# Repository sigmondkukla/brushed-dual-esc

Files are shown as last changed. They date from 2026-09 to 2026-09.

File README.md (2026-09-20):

# brushed-dual-esc
**Clarkson University Combat Robotics SPEED Team**

## Summary

Dual drive ESC for Clarkson Combat Robotics 1lb freshman PLAnt competition.
Supports two 3A brushed drive motors and includes a 5V 1A BEC output to power a receiver. 

## Details

The ESC implements an STM32C011 MCU to generate PWM for motor drivers from RX channel inputs while monitoring current, signal prescence (failsafe), and battery voltage UVLO.

With the 2026 revision of the ESC, XT30 wire-to-board connectors have been replaced with solder pads for leads to GNB A30 connectors.
An XT30 connector is still reccomended for the battery input.
The battery shall be a 2S or 3S LiPo battery; 4S is not supported based on cost optimization, though targeting a slightly higher cost (and larger size) by increasing capacitor specifications is a simple modification.
At 4S, the current from the 5V BEC output shall be kept to a minimum. 

The ESC expects two receiver channel outputs to be connected to the CH1 and CH2 inputs, which map directly to the DRV1 and DRV2 outputs. A 50 Hz (20 ms period) PWM signal (5V tolerated) with a duty cycle between 1000 us and 2000 us is needed, based on the outputs of the common FS-2A receiver.
A duty cycle of 1500 us is considered neutral, with lower duty cycles resulting in reverse operation and higher duty cycles corresponding to forward operation.

A 3A current limit has been configured with the 750-ohm resistors connected to IPROPI on each motor driver.
Above this current limit, the ESC will chop to avoid over current, despite the driver supporting up to 3.7A.
The ESC pairs well therefore with the [Repeat Mini Brushed Mk2](https://repeat-robotics.com/products/repeat-mini-brushed-mk2-1pcs), which has a stall current of 2A at 3S.

## Assembly

Assembly with a pick-and-place machine is reccomended for large volumes >= 10 units, though hand assembly is straightforward given the large motor driver, LDO, and passives packages.
The pick and place work file for a CHM-T36VA machine is included in the `pcb/fabrication` directory, though minor modifications may be necessary.
The DRV8231 ICs were not successfully picked by the machine so are set to be skipped, and the electrolytic capacitors were not attempted.
I loaded the 503 nozzle in tool 1 and the 505 nozzle in tool 2 for this job.

A clean paste image is necessary for successful soldering of the STM32 MCU.

## Programming

Programming is achieved through a Tag-Connect TC2030-CTX-NL pogo pins programmer cable which retails around $50, though can be purchased on Aliexpress for about half the price.
I'm using it in conjunction with a Segger J-Link EDU mini though any debugger can be used.
SWO is not available on STM32C0 so one of the six pins is unused.

The firmware may be programmed using [STM32CubeProg](https://www.st.com/en/development-tools/stm32cubeprog.html) and the firmware ELF file included in the most recent release on GitHub.

## Images
### Screenshots
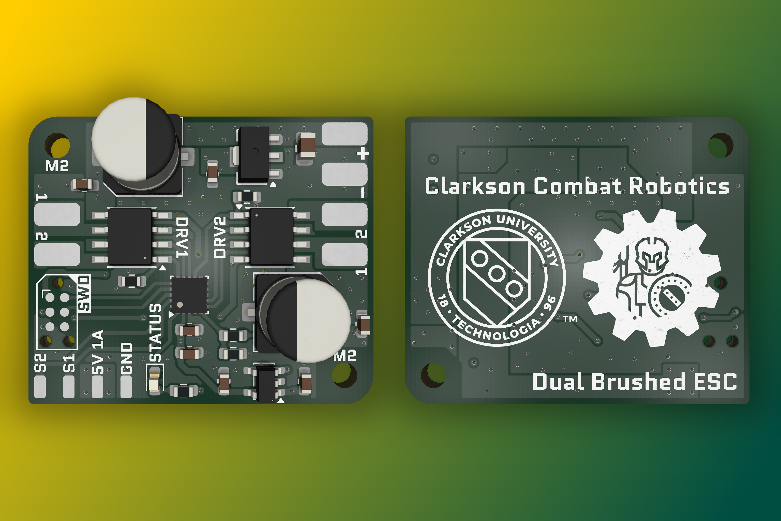
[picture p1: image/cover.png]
Cover

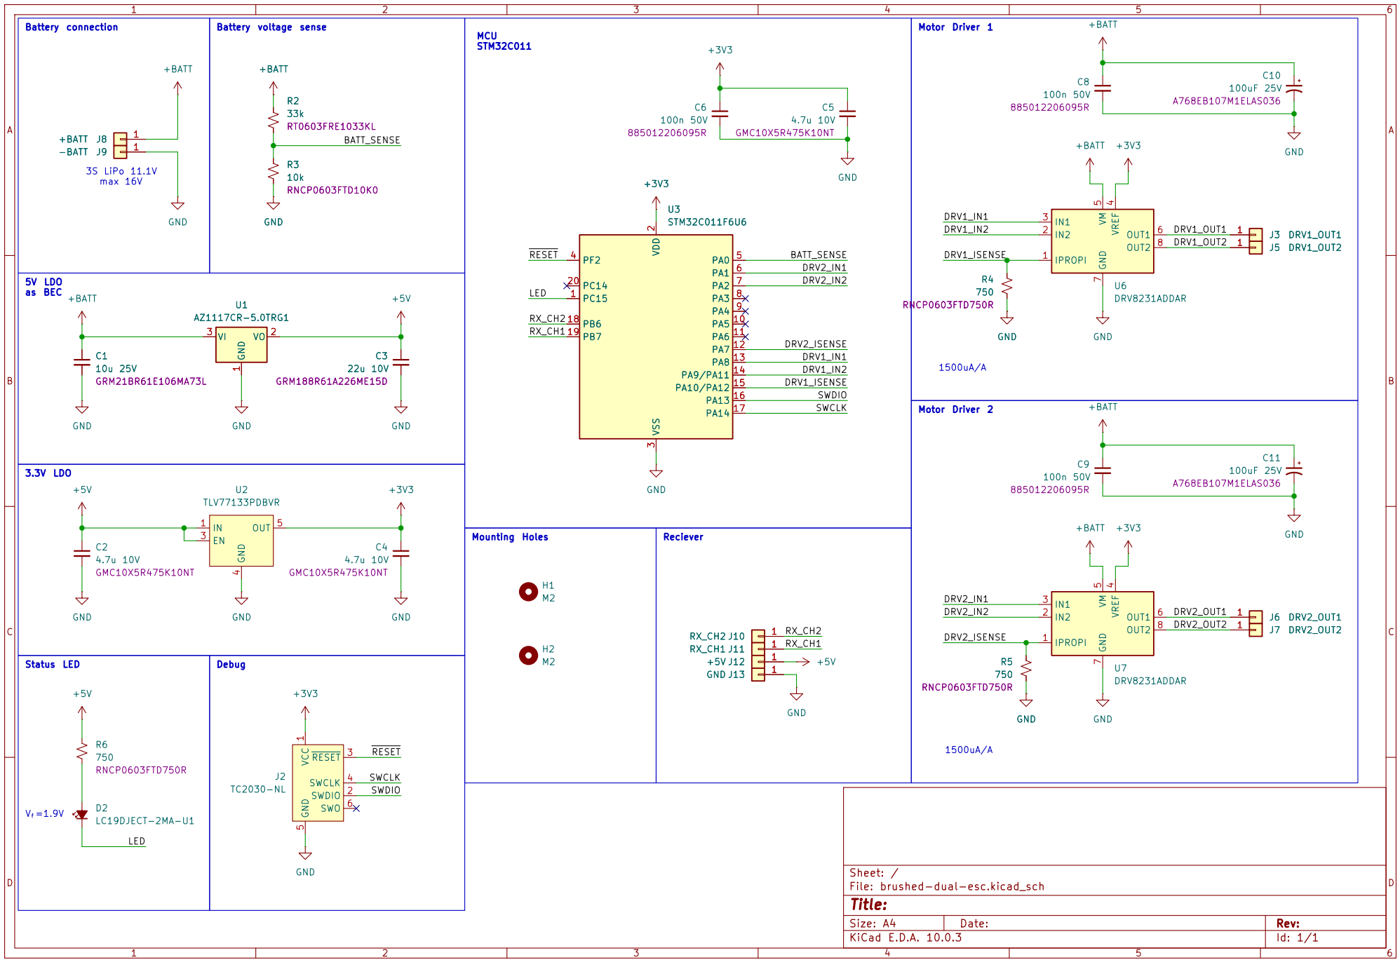
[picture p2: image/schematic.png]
Schematic diagram

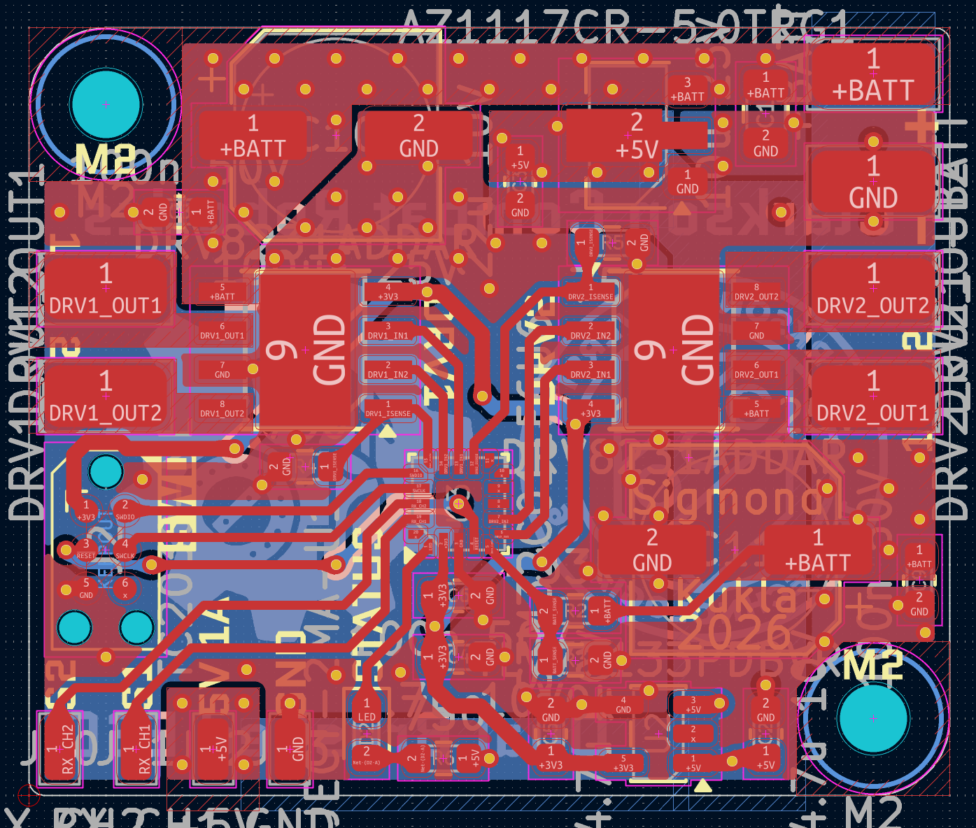
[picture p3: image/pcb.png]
PCB top layer


### Photos
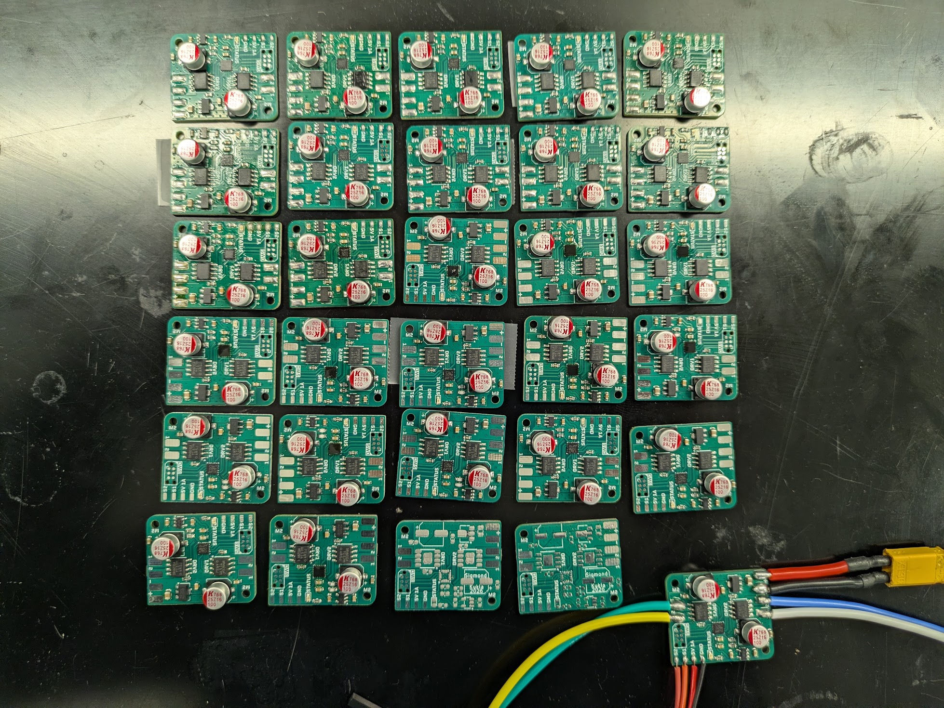
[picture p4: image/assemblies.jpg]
Assemblies


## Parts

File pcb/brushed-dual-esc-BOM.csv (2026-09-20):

Reference | Qty | Value | MPN
C1 | 1 | 10µF 25V | GRM21BR61E106MA73L
C2,C4,C5 | 3 | 4.7u 10V | GMC10X5R475K10NT
C3 | 1 | 22uF 10V | GRM188R61A226ME15D
C6,C8,C9 | 3 | 100n 50V | 885012206095R
C10,C11 | 2 | 100uF 25V | A768EB107M1ELAS036
D2 | 1 | Vf=1.9V | LC19DJECT-2MA-U1
R2 | 1 | 33k | RT0603FRE1033KL
R3 | 1 | 10k | RNCP0603FTD10K0
R4,R5,R6 | 3 | 750 | RNCP0603FTD750R
U1 | 1 | AZ1117CR-5.0TRG1 | AZ1117CR-5.0TRG1
U2 | 1 | TLV77133PDBVR | TLV77133PDBVR
U3 | 1 | STM32C011F6U6 | STM32C011F6U6
U6,U7 | 2 | DRV8231ADDAR | DRV8231ADDAR

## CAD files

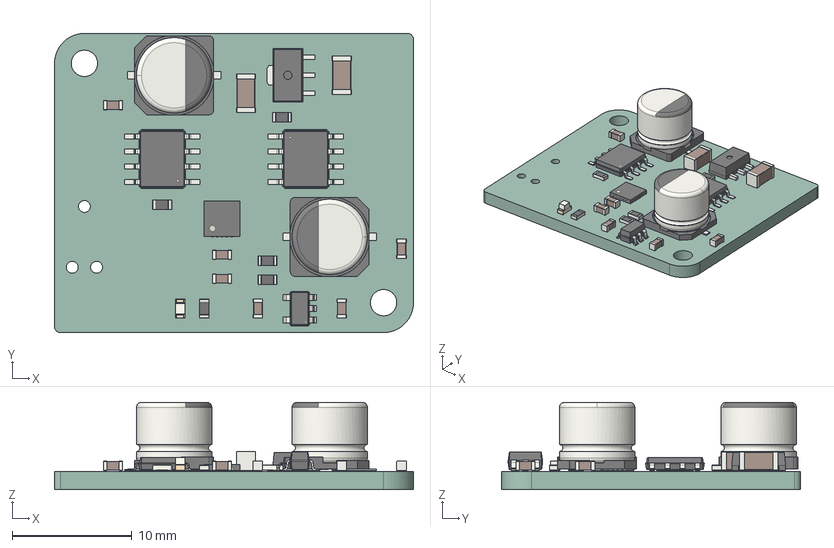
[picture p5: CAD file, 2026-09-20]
pcb/brushed-dual-esc.step
30.0 x 25.0 x 7.29 mm
R_0603_1608Metric x 5
C_0603_1608Metric x 6
CP_Elec_63x57 x 2
HSOP-8-1EP_3.9x4.9mm_P1.27mm_EP2.41x3.1mm x 2
LED_0603_1608Metric
SOT-23-5
C_1206_3216Metric x 2
UQFN-20-1EP_3x3mm_Pitch0.4mm
adbeea57-9c39-11ed-93f0-dde97e994e83_part
adbeea58-9c39-11ed-93f0-dde97e994e83_part
adbeea59-9c39-11ed-93f0-dde97e994e83_part
brushed-dual-esc_PCB

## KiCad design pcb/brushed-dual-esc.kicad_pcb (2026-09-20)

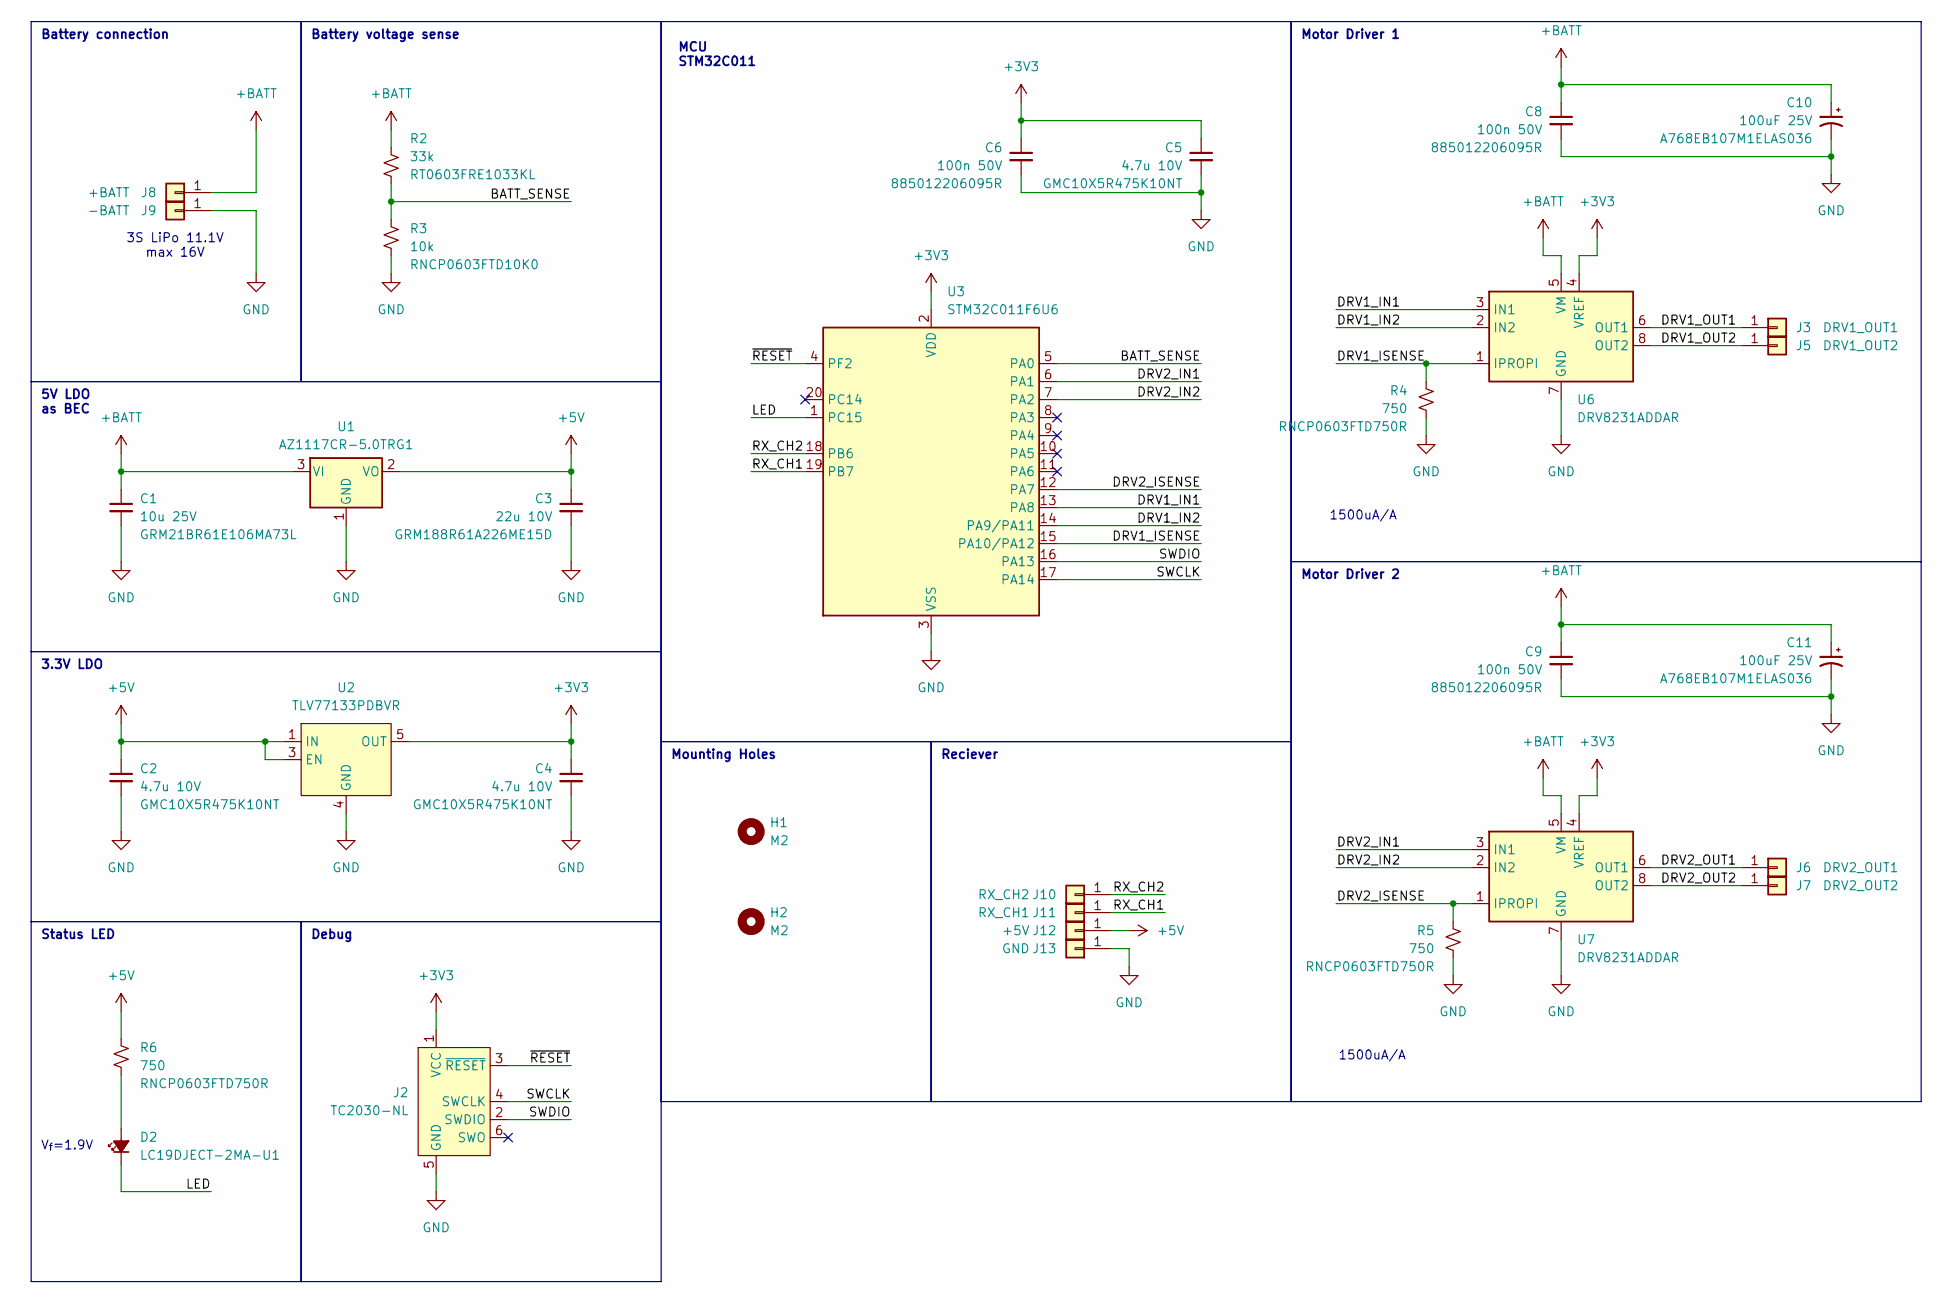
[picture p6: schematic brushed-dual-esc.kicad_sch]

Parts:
C1: 10u 25V; C_0805_2012Metric; MPN GRM21BR61E106MA73L
C2, C4, C5: 4.7u 10V; C_0603_1608Metric; MPN GMC10X5R475K10NT
C3: 22u 10V; C_0603_1608Metric; MPN GRM188R61A226ME15D
C6, C8, C9: 100n 50V; C_0603_1608Metric; MPN 885012206095R
C10, C11: 100uF 25V; CP_Elec_6.3x5.7; MPN A768EB107M1ELAS036
D2: LC19DJECT-2MA-U1; LED_0603_1608Metric; MPN LC19DJECT-2MA-U1
H1, H2: M2; MountingHole_2.2mm_M2
J2: TC2030-NL; Tag-Connect_TC2030-IDC-NL_2x03_P1.27mm_Vertical
J3: DRV1_OUT1; SolderWirePad_1x01_SMD_2x4mm
J5: DRV1_OUT2; SolderWirePad_1x01_SMD_2x4mm
J6: DRV2_OUT1; SolderWirePad_1x01_SMD_2x4mm
J7: DRV2_OUT2; SolderWirePad_1x01_SMD_2x4mm
J8: +BATT; SolderWirePad_1x01_SMD_2x4mm
J9: -BATT; SolderWirePad_1x01_SMD_2x4mm
J10: RX_CH2; SolderWirePad_1x01_SMD_1x2mm
J11: RX_CH1; SolderWirePad_1x01_SMD_1x2mm
J12: +5V; SolderWirePad_1x01_SMD_1x2mm
J13: GND; SolderWirePad_1x01_SMD_1x2mm
R2: 33k; R_0603_1608Metric; MPN RT0603FRE1033KL
R3: 10k; R_0603_1608Metric; MPN RNCP0603FTD10K0
R4, R5, R6: 750; R_0603_1608Metric; MPN RNCP0603FTD750R
U1: AZ1117CR-5.0TRG1; SOT-89-3; MPN AZ1117CR-5.0TRG1
U2: TLV77133PDBVR; SOT-23-5; MPN TLV77133PDBVR
U3: STM32C011F6U6; ST_UFQFPN-20_3x3mm_P0.5mm; MPN STM32C011F6U6
U6, U7: DRV8231ADDAR; Texas_HSOP-8-1EP_3.9x4.9mm_P1.27mm; MPN DRV8231ADDAR

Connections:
+3V3: C4.1, C5.1, C6.1, J2.1 (VCC), U2.5 (OUT), U3.2 (VDD), U6.4 (VREF), U7.4 (VREF)
+5V: C2.1, C3.1, J12.1 (Pin_1_1), R6.1, U1.2 (VO), U2.1 (IN), U2.3 (EN)
+BATT: C1.1, C8.1, C9.1, C10.1, C11.1, J8.1 (Pin_1_1), R2.1, U1.3 (VI), U6.5 (VM), U7.5 (VM)
/BATT_SENSE: R2.2, R3.1, U3.5 (PA0)
/DRV1_IN1: U3.13 (PA8), U6.3 (IN1)
/DRV1_IN2: U3.14 (PA9/PA11), U6.2 (IN2)
/DRV1_ISENSE: R4.1, U3.15 (PA10/PA12), U6.1 (IPROPI)
/DRV1_OUT1: J3.1 (Pin_1_1), U6.6 (OUT1)
/DRV1_OUT2: J5.1 (Pin_1_1), U6.8 (OUT2)
/DRV2_IN1: U3.6 (PA1), U7.3 (IN1)
/DRV2_IN2: U3.7 (PA2), U7.2 (IN2)
/DRV2_ISENSE: R5.1, U3.12 (PA7), U7.1 (IPROPI)
/DRV2_OUT1: J6.1 (Pin_1_1), U7.6 (OUT1)
/DRV2_OUT2: J7.1 (Pin_1_1), U7.8 (OUT2)
/LED: D2.1 (K), U3.1 (PC15)
/RX_CH1: J11.1 (Pin_1_1), U3.19 (PB7)
/RX_CH2: J10.1 (Pin_1_1), U3.18 (PB6)
/SWCLK: J2.4 (SWCLK), U3.17 (PA14)
/SWDIO: J2.2 (SWDIO), U3.16 (PA13)
/~RESET: J2.3 (~RESET), U3.4 (PF2)
GND: C1.2, C2.2, C3.2, C4.2, C5.2, C6.2, C8.2, C9.2, C10.2, C11.2, J2.5 (GND), J9.1 (Pin_1_1), J13.1 (Pin_1_1), R3.2, R4.2, R5.2, U1.1 (GND), U2.4 (GND), U3.3 (VSS), U6.7 (GND), U6.9 (GND), U7.7 (GND), U7.9 (GND)
unnamed: D2.2 (A), R6.2

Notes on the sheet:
3.3V LDO
Status LED
Motor Driver 1
Motor Driver 2
Mounting Holes
1500uA/A
5V LDO as BEC
V_{f}=1.9V
Battery connection
Battery voltage sense
MCU STM32C011
3S LiPo 11.1V max 16V
Reciever
Debug

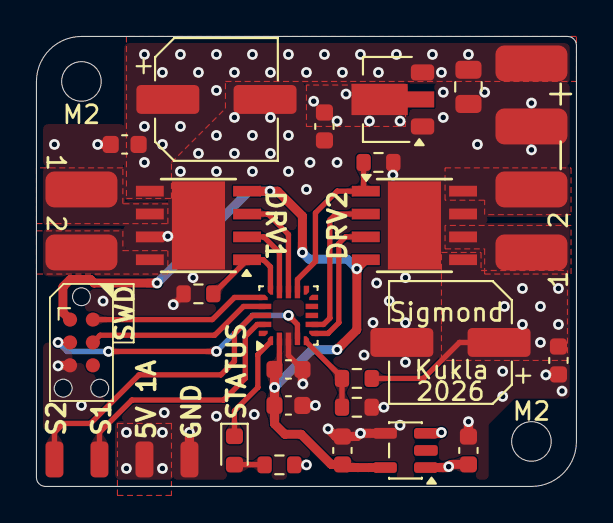
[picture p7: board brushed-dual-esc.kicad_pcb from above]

Board: 2 copper layers, 30.0 x 25.0 mm, 34 parts (0 on the bottom side), 22 nets.

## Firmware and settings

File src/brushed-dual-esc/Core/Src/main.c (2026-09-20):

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
/* Includes ------------------------------------------------------------------*/
#include "main.h"

/* USER CODE BEGIN PD */
// Failsafe configuration
#define PULSE_TIMEOUT_MS 100 // 100 ms at 50 Hz is 5 missed pulses I think

// UVLO configuration
// Calculate this yourself:
// 1. Multiply min cell voltage by number of cells to get min battery voltage
// 		v_batt_min = v_cell_min * batt_s
// 2. Calculate voltage divider gain based on R1 and R2 in https://www.digikey.com/en/resources/conversion-calculators/conversion-calculator-voltage-divider
// 		divider_gain = r2 / (r1 + r2)
// 3. Calculate min divided voltage (input to ADC pin)
// 		v_divided_min = v_batt_min * divider_gain
// 4. Calculate min ADC counts (here we assume 12 bit ADC, so (2^12)-1=4095 max counts at VREF, which we assume is 3.3V)
// 		MIN_BATT_ADC = (v_divided_min / 3.3) * 4095
// 5. Round it to the nearest whole number and enter below
#define MIN_BATT_ADC 2597 // 3V/cell

// pulse limits; discard invalid pulses beyond this
// based on FS-2A 1000-2000us
#define PULSE_INVALID_MIN 800 // [us]
#define PULSE_INVALID_MAX 2200 // [us]
/* USER CODE END PD */

ADC_HandleTypeDef hadc1;
DMA_HandleTypeDef hdma_adc1;

TIM_HandleTypeDef htim1;
TIM_HandleTypeDef htim3;

/* USER CODE BEGIN PV */
// RX_CH1 = TIM3_CH1 -> DRV1
volatile uint32_t IC_Val1_CH1 = 0;
volatile uint32_t IC_Val2_CH1 = 0;
volatile uint32_t Pulse_Width_CH1 = 1500; // default to neutral
volatile uint8_t Is_First_Captured_CH1 = 0; // 0 = waiting for rising, 1 = waiting for falling
volatile uint32_t last_pulse_time_ch1 = 0; // For failsafe

// RX_CH2 = TIM3_CH2 -> DRV2
volatile uint32_t IC_Val1_CH2 = 0;
volatile uint32_t IC_Val2_CH2 = 0;
volatile uint32_t Pulse_Width_CH2 = 1500; // default to neutral
volatile uint8_t Is_First_Captured_CH2 = 0; // 0 = waiting for rising, 1 = waiting for falling
volatile uint32_t last_pulse_time_ch2 = 0; // For failsafe

volatile uint32_t now;
uint32_t pulse1, pulse2;
uint32_t last_seen1, last_seen2;
uint8_t error;
uint8_t batt_cutoff;
volatile uint32_t batt_sense = 69;
volatile uint32_t adc_buf[3]; // BATT_SENSE, DRV2_ISENSE, DRV1_ISENSE
/* USER CODE END PV */

void SystemClock_Config(void);
static void MX_GPIO_Init(void);
static void MX_DMA_Init(void);
static void MX_ADC1_Init(void);
static void MX_TIM1_Init(void);
static void MX_TIM3_Init(void);
/* USER CODE BEGIN PFP */
void set_motor_speed(uint32_t pulse, uint32_t tim_channel_in1, uint32_t tim_channel_in2);
/* USER CODE END PFP */

/**
  * @brief  The application entry point.
  * @retval int
  */
int main(void)
{

  /* MCU Configuration--------------------------------------------------------*/

  /* Reset of all peripherals, Initializes the Flash interface and the Systick. */
  HAL_Init();

  /* Configure the system clock */
  SystemClock_Config();

  /* Initialize all configured peripherals */
  MX_GPIO_Init();
  MX_DMA_Init();
  MX_ADC1_Init();
  MX_TIM1_Init();
  MX_TIM3_Init();
  /* USER CODE BEGIN 2 */

	HAL_GPIO_WritePin(LED_GPIO_Port, LED_Pin, 0); // indicate boot by flashing LED 1 on

	// start PWM outputs for DRV1
	HAL_TIM_PWM_Start(&htim1, TIM_CHANNEL_1);
	HAL_TIM_PWM_Start(&htim1, TIM_CHANNEL_4);

	// start PWM outputs for DRV2
	HAL_TIM_PWM_Start(&htim1, TIM_CHANNEL_2);
	HAL_TIM_PWM_Start(&htim1, TIM_CHANNEL_3);

	// set all drives to coast
	__HAL_TIM_SET_COMPARE(&htim1, TIM_CHANNEL_1, 0);
	__HAL_TIM_SET_COMPARE(&htim1, TIM_CHANNEL_2, 0);
	__HAL_TIM_SET_COMPARE(&htim1, TIM_CHANNEL_3, 0);
	__HAL_TIM_SET_COMPARE(&htim1, TIM_CHANNEL_4, 0);

	// start input capture interrupts for RX
	HAL_TIM_IC_Start_IT(&htim3, TIM_CHANNEL_1);
	HAL_TIM_IC_Start_IT(&htim3, TIM_CHANNEL_2);

	// start ADC in continuous DMA mode
	HAL_ADCEx_Calibration_Start(&hadc1);
	HAL_ADC_Start_DMA(&hadc1, (uint32_t*)adc_buf, 3);

	// init failsafe
	now = HAL_GetTick();
	last_pulse_time_ch1 = now;
	last_pulse_time_ch2 = now;
	error = 0;
	batt_cutoff = 0;

	// Turn off LED to indicate success
	HAL_GPIO_WritePin(LED_GPIO_Port, LED_Pin, 1); // turn off LED to indicate etup success

  /* USER CODE END 2 */

  /* Infinite loop */
  /* USER CODE BEGIN WHILE */
  while (1)
  {
    /* USER CODE END WHILE */

    /* USER CODE BEGIN 3 */
	now = HAL_GetTick();
	error = 0;

	// UVLO
	batt_sense = adc_buf[0];
	// drv2_isense = adc_buf[1];
	// drv1_isense = adc_buf[2];

	if (batt_sense < MIN_BATT_ADC) {
		batt_cutoff = 1;
		error = 1;
	} else {
		batt_cutoff = 0;
	}

	// Atomically get the latest pulse data from the ISR
	HAL_NVIC_DisableIRQ(TIM3_IRQn);
	pulse1 = Pulse_Width_CH1;
	last_seen1 = last_pulse_time_ch1;
	pulse2 = Pulse_Width_CH2;
	last_seen2 = last_pulse_time_ch2;
	HAL_NVIC_EnableIRQ(TIM3_IRQn);

	if (!batt_cutoff) { // if there is sufficient battery voltage
		if (now - last_seen1 > PULSE_TIMEOUT_MS) // if RX channel for motor 1 failsafed
		{
			// coast IN1=IN2=0
			__HAL_TIM_SET_COMPARE(&htim1, TIM_CHANNEL_1, 0);
			__HAL_TIM_SET_COMPARE(&htim1, TIM_CHANNEL_4, 0);

			error = 1;
		}
		else // motor 1 good
		{
			set_motor_speed(pulse1, TIM_CHANNEL_1, TIM_CHANNEL_4);
		}

		if (now - last_seen2 > PULSE_TIMEOUT_MS) // if RX channel for motor 2 failsafed
		{
			// coast IN1=IN2=0
			__HAL_TIM_SET_COMPARE(&htim1, TIM_CHANNEL_2, 0);
			__HAL_TIM_SET_COMPARE(&htim1, TIM_CHANNEL_3, 0);

			error = 1;
		}
		else // motor 2 good
		{
			set_motor_speed(pulse2, TIM_CHANNEL_2, TIM_CHANNEL_3);
		}
	}

	// write error state to LED each time
	HAL_GPIO_WritePin(LED_GPIO_Port, LED_Pin, !error);
  }
  /* USER CODE END 3 */
}

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
/* USER CODE BEGIN 4 */
/**
  * @brief  Converts a 1000-2000us pulse to motor driver PWM outputs
  * @param  pulse: The measured pulse width in microseconds (1000-2000)
  * @param  tim_channel_in1: The TIM1 channel for the driver's IN1 pin
  * @param  tim_channel_in2: The TIM1 channel for the driver's IN2 pin
  * @retval None
  */
void set_motor_speed(uint32_t pulse, uint32_t tim_channel_in1, uint32_t tim_channel_in2)
{
    uint32_t duty = 0;
    const uint32_t MAX_DUTY = 2399; // from htim1.Init.Period
    // deadzone
    const uint32_t NEUTRAL_LOW = 1450;
    const uint32_t NEUTRAL_HIGH = 1550;
    const uint32_t MIN_PULSE = 1000;
    const uint32_t MAX_PULSE = 2000;

    if (pulse < PULSE_INVALID_MIN || pulse > PULSE_INVALID_MAX) // pulse out of range so default to neutral
    {
    	pulse = 1500;
    	error = 1;
    }

    // Channel neutral coast
    // (DRV8231A Table 8-2: IN1=0, IN2=0 -> Coast)
//    if (pulse > NEUTRAL_LOW && pulse < NEUTRAL_HIGH)
//    {
//        __HAL_TIM_SET_COMPARE(&htim1, tim_channel_in1, 0);
//        __HAL_TIM_SET_COMPARE(&htim1, tim_channel_in2, 0);
//    }

    // Channel neutral brake
    // (DRV8231A Table 8-2: IN1=0, IN2=0 -> Coast)
    if (pulse > NEUTRAL_LOW && pulse < NEUTRAL_HIGH)
    {
        __HAL_TIM_SET_COMPARE(&htim1, tim_channel_in1, MAX_DUTY);
        __HAL_TIM_SET_COMPARE(&htim1, tim_channel_in2, MAX_DUTY);
    }

    // Channel forward
    // (DRV8231A Table 8-2: IN1=PWM, IN2=0 -> Forward)
    else if (pulse >= NEUTRAL_HIGH)
    {
        if(pulse > MAX_PULSE) pulse = MAX_PULSE;

        // Map [1550...2000] to [0...599]
        duty = (pulse - NEUTRAL_HIGH) * MAX_DUTY / (MAX_PULSE - NEUTRAL_HIGH);
        if (duty > MAX_DUTY) duty = MAX_DUTY;

        __HAL_TIM_SET_COMPARE(&htim1, tim_channel_in1, duty); // IN1 = PWM
        __HAL_TIM_SET_COMPARE(&htim1, tim_channel_in2, 0);    // IN2 = 0
    }

    // Channel reverse
    // (DRV8231A Table 8-2: IN1=0, IN2=PWM -> Reverse)
    else if (pulse <= NEUTRAL_LOW)
    {
        if(pulse < MIN_PULSE) pulse = MIN_PULSE;

        // Map [1450...1000] to [0...599]
        duty = (NEUTRAL_LOW - pulse) * MAX_DUTY / (NEUTRAL_LOW - MIN_PULSE);
        if (duty > MAX_DUTY) duty = MAX_DUTY;

        __HAL_TIM_SET_COMPARE(&htim1, tim_channel_in1, 0);    // IN1 = 0
        __HAL_TIM_SET_COMPARE(&htim1, tim_channel_in2, duty); // IN2 = PWM
    }
}

/**
  * @brief  Input Capture callback in non-blocking mode
  * @param  htim: TIM handle
  * @retval None
  */
void HAL_TIM_IC_CaptureCallback(TIM_HandleTypeDef *htim)
{
    if (htim->Instance == TIM3) // TIM3 used for RX channel input capture
    {
        if (htim->Channel == HAL_TIM_ACTIVE_CHANNEL_1) // RX_CH1, TIM3_CH1, will eventually map to DRV1
        {
            if (Is_First_Captured_CH1 == 0) // first edge (rising)
            {
                IC_Val1_CH1 = HAL_TIM_ReadCapturedValue(htim, TIM_CHANNEL_1);
                Is_First_Captured_CH1 = 1; // mark that we captured rising edge
                __HAL_TIM_SET_CAPTUREPOLARITY(htim, TIM_CHANNEL_1, TIM_INPUTCHANNELPOLARITY_FALLING); // capture falling edge next
            }
            else // on second edge (falling)
            {
                IC_Val2_CH1 = HAL_TIM_ReadCapturedValue(htim, TIM_CHANNEL_1);
                // --- FIX: Use a unique variable name ---
                uint32_t new_pulse_width_ch1 = 0;

                if (IC_Val2_CH1 > IC_Val1_CH1)
                {
                    new_pulse_width_ch1 = IC_Val2_CH1 - IC_Val1_CH1;
                }
                else if (IC_Val1_CH1 > IC_Val2_CH1) // Timer overflow
                {
                    new_pulse_width_ch1 = (0xFFFF - IC_Val1_CH1) + IC_Val2_CH1 + 1;
                }

                // --- Validate and save for CH1 ---
                // Discard any junk pulses outside the valid 800-2200us range
                if (new_pulse_width_ch1 > PULSE_INVALID_MIN && new_pulse_width_ch1 < PULSE_INVALID_MAX)
                {
                    Pulse_Width_CH1 = new_pulse_width_ch1; // Write to CH1's variable
                    last_pulse_time_ch1 = HAL_GetTick();   // Write to CH1's timestamp
                }

                Is_First_Captured_CH1 = 0;
                // Change polarity back to rising edge
                __HAL_TIM_SET_CAPTUREPOLARITY(htim, TIM_CHANNEL_1, TIM_INPUTCHANNELPOLARITY_RISING);
            }
        }

        if (htim->Channel == HAL_TIM_ACTIVE_CHANNEL_2) // RX_CH2, TIM3_CH2 will eventually map to DRV2
        {
            if (Is_First_Captured_CH2 == 0) // First edge (Rising)
            {
                IC_Val1_CH2 = HAL_TIM_ReadCapturedValue(htim, TIM_CHANNEL_2);
                Is_First_Captured_CH2 = 1;
                // Change polarity to falling edge
                __HAL_TIM_SET_CAPTUREPOLARITY(htim, TIM_CHANNEL_2, TIM_INPUTCHANNELPOLARITY_FALLING);
            }
            else  // Second edge (Falling)
            {
                IC_Val2_CH2 = HAL_TIM_ReadCapturedValue(htim, TIM_CHANNEL_2);
                // --- FIX: Use a unique variable name ---
                uint32_t new_pulse_width_ch2 = 0;

                if (IC_Val2_CH2 > IC_Val1_CH2)
                {
                    new_pulse_width_ch2 = IC_Val2_CH2 - IC_Val1_CH2;
                }
                else if (IC_Val1_CH2 > IC_Val2_CH2) // Timer overflow
                {
                    new_pulse_width_ch2 = (0xFFFF - IC_Val1_CH2) + IC_Val2_CH2 + 1;
                }

                // --- Validate and save for CH2 ---
                // Discard any junk pulses outside the valid 800-2200us range
                if (new_pulse_width_ch2 > PULSE_INVALID_MIN && new_pulse_width_ch2 < PULSE_INVALID_MAX)
                {
                    Pulse_Width_CH2 = new_pulse_width_ch2; // Write to CH2's variable
                    last_pulse_time_ch2 = HAL_GetTick();   // Write to CH2's timestamp
                }

                Is_First_Captured_CH2 = 0;
                // Change polarity back to rising edge
                __HAL_TIM_SET_CAPTUREPOLARITY(htim, TIM_CHANNEL_2, TIM_INPUTCHANNELPOLARITY_RISING);
            }
        }
    }
}
/* USER CODE END 4 */
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


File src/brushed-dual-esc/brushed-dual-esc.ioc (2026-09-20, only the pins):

Mcu.UserName=STM32C011F6Ux
PA0.GPIO_Label=BATT_SENSE
PA0.Signal=ADC1_IN0
PA1.GPIO_Label=DRV2_IN1
PA1.Signal=S_TIM1_CH2
PA13.Signal=DEBUG_SWDIO
PA14-BOOT0.Signal=DEBUG_SWCLK
PA2.GPIO_Label=DRV2_IN2
PA2.Signal=S_TIM1_CH3
PA7.GPIO_Label=DRV2_ISENSE
PA7.Signal=ADC1_IN7
PA8.GPIO_Label=DRV1_IN1
PA8.Signal=S_TIM1_CH1
PB6.GPIO_Label=RX_CH2
PB6.Signal=S_TIM3_CH2
PB7.GPIO_Label=RX_CH1
PB7.Signal=S_TIM3_CH1

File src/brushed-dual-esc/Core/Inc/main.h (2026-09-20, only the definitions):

#define LED_Pin GPIO_PIN_15
#define LED_GPIO_Port GPIOC
#define BATT_SENSE_Pin GPIO_PIN_0
#define BATT_SENSE_GPIO_Port GPIOA
#define DRV2_IN1_Pin GPIO_PIN_1
#define DRV2_IN1_GPIO_Port GPIOA
#define DRV2_IN2_Pin GPIO_PIN_2
#define DRV2_IN2_GPIO_Port GPIOA
#define DRV2_ISENSE_Pin GPIO_PIN_7
#define DRV2_ISENSE_GPIO_Port GPIOA
#define DRV1_IN1_Pin GPIO_PIN_8
#define DRV1_IN1_GPIO_Port GPIOA
#define DRV1_IN2_Pin GPIO_PIN_11
#define DRV1_IN2_GPIO_Port GPIOA
#define DRV1_ISENSE_Pin GPIO_PIN_12
#define DRV1_ISENSE_GPIO_Port GPIOA
#define RX_CH2_Pin GPIO_PIN_6
#define RX_CH2_GPIO_Port GPIOB
#define RX_CH1_Pin GPIO_PIN_7
#define RX_CH1_GPIO_Port GPIOB

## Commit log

2025-08-24 Finish design
    [brushed-dual-esc.kicad_pcb, brushed-dual-esc.kicad_sch, motor_driver.kicad_sch]
2025-08-26 Add status LED on spare pin
    [brushed-dual-esc.kicad_pcb, brushed-dual-esc.kicad_sch]
2025-08-26 Create 3V3 zone in top left
    [brushed-dual-esc.kicad_pcb]
2025-08-26 Adjust 5V LDO ground plane placement
    [brushed-dual-esc.kicad_pcb]
2025-08-26 Increase top GND zone size for LDO
    [brushed-dual-esc.kicad_pcb]
2025-08-27 Fix capacitor siutation
    [brushed-dual-esc.kicad_pcb, brushed-dual-esc.kicad_sch]
2025-08-27 Update footprints
2025-08-27 Add testpoints and imrpove silkscreen
    [brushed-dual-esc.kicad_pcb, brushed-dual-esc.kicad_sch]
2025-09-18 Add step file
    [bom.csv, brushed-dual-esc.kicad_pcb, brushed-dual-esc.kicad_sch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]
2025-10-26 Semi-working ESC firmware

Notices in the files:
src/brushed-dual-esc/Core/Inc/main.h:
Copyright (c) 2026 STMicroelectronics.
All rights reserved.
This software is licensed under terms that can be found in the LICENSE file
